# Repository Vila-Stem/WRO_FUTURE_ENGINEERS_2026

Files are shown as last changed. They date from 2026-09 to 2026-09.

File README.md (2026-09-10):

# VILA-STEM 8’s repository
**This is the Vila-stem 8 repository for the 2026 season WRO Future Engineers challenge**

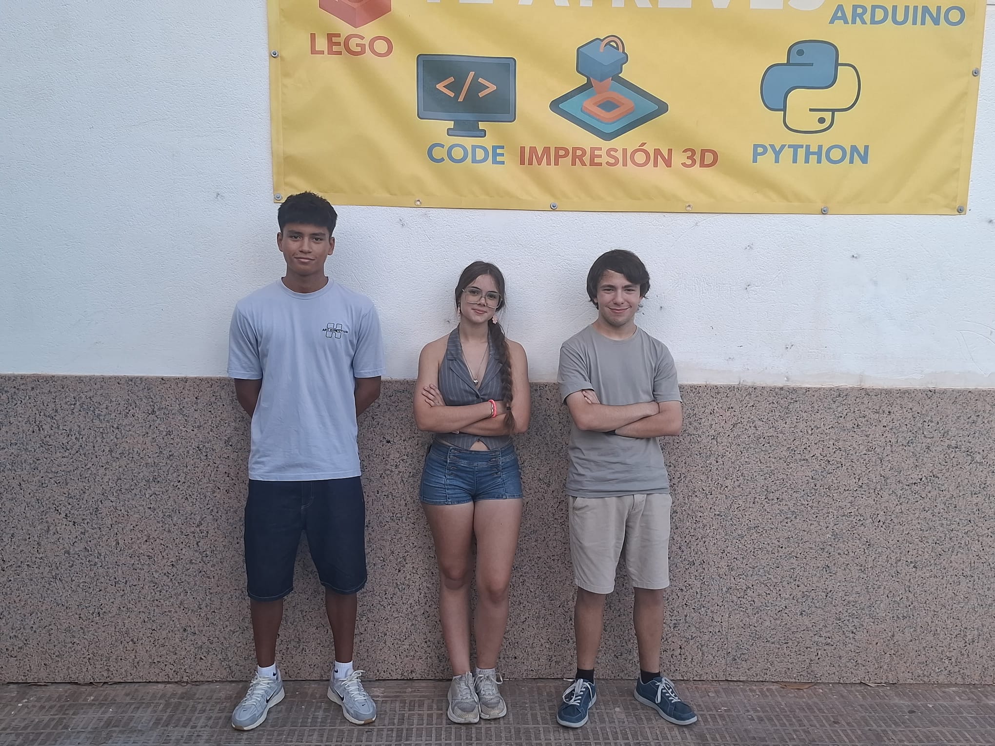
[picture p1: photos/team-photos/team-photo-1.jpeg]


## TABLE OF CONTENTS

* [1. INTRODUCTION](#1-introduction)

* [2. MOBILITY MANAGEMENT](#2-mobility-management)
    * [2.1. Chassis design](#21-chassis-design)
    * [2.2. How we arrived at this design](#22-how-we-arrived-at-this-design)
    * [2.3. Drive System](#23-drive-system)
    * [2.4. Steering System](#24-steering-system)

* [3. SENSORS AND ELECTRICITY](#3-sensors-and-electricity)
    * [3.1. List of sensors and electrical components](#31-list-of-sensors-and-electrical-components)
    * [3.2. Electrical diagram](#32-electrical-diagram)
    * [3.3. Connection type diagram](#33-connection-type-diagram)
    * [3.4. Power consumption](#34-power-consumption)

* [4. CODE](#4-code)

* [5. PHOTOS](#5-photos)
    * [5.1. Robot photos](#51-robot-photos)
    * [5.2. Team photos](#52-team-photos)

* [6. VIDEOS](#6-videos)

* [7. LIST OF COMPONENTS](#7-list-of-components)

* [8. LICENSE](#8-license)

* [9. ENGINEERING JOURNAL](#9-engineering-journal)

## 1. INTRODUCTION

Vila-stem 8 is the Future Engineers team of the Vila-Stem educational robotics cultural association, located in Vila-real, Spain. Some members of this team have already participated in the WRO in different categories in previous years, including this year, while for others it is their first time competing, but we are all equally excited to participate in the Future Engineers category of WRO 2026.

Our first competition this season was the regional WRO in Dénia, where we won first place and qualified for the national final.

Now we are heading to the national final of WRO Spain 2026 in Andorra, eager to present our project.

Throughout this document, you will find an explanation of our robot and links to other documents that explain the different sections in more detail.

To comply with the competition rules, we have also included a [**Engineering Journal**](/engineering-journal.pdf) in PDF format. This document is a compilation of the information explained throughout this repository.

## 2. MOBILITY MANAGEMENT

### 2.1. Chassis design

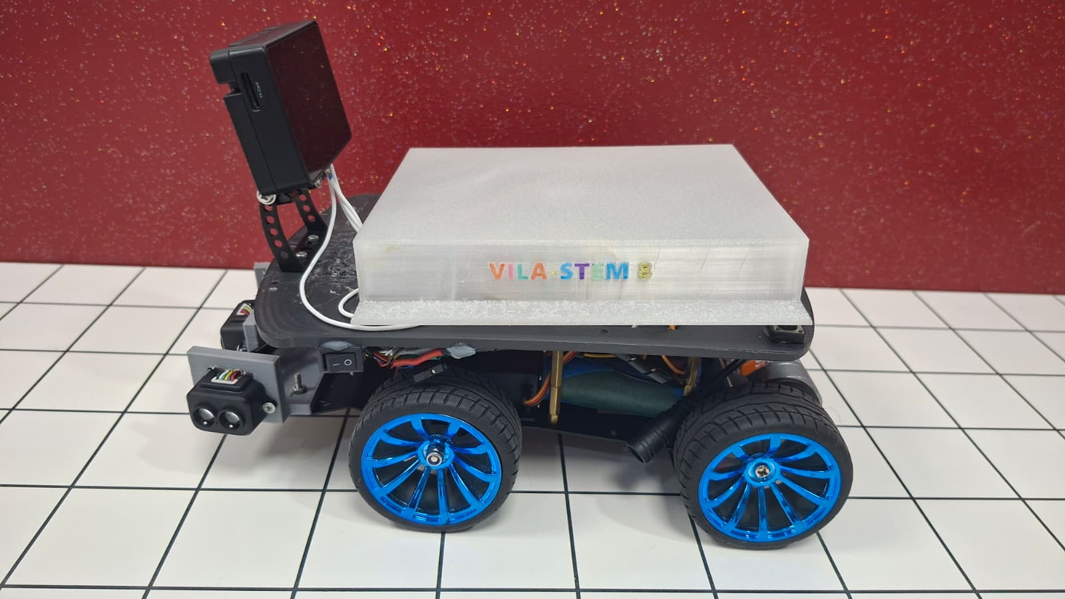
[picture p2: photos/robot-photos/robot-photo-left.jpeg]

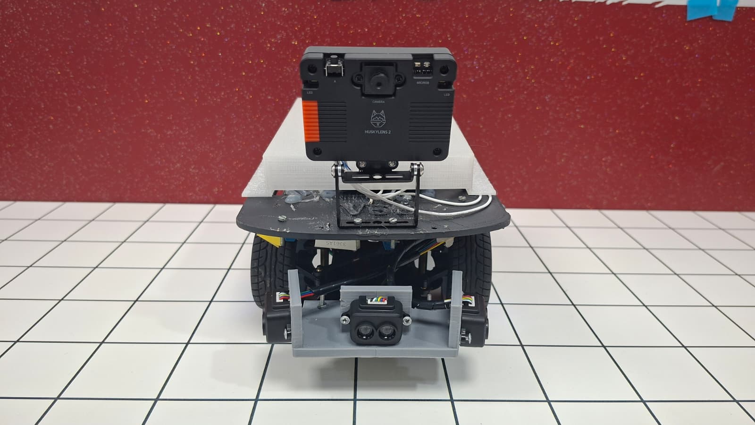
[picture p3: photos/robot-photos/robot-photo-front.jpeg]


The lower chassis base comes from a development kit we acquired, so we simply had to assemble it. This kit provided the wheels, motor, and steering system, which simplified assembly. We designed a top platform on top of this kit, where the components are installed, as well as another set of parts to mount the components.

Purchasing this kit allowed us to have a metal chassis that better withstands the robot's stresses. This freed us up to design, using plastic and 3D printing, those parts that wouldn't be subjected to heavy loads.

### 2.2. How we arrived at this design

Initially, the idea was to mount all the components on the lower chassis, but the lack of space and the desire for a more aesthetically pleasing design led us to install a top platform. This platform saves space and also provides easier access to the connections. We ruled out increasing the robot's height because this keeps the center of gravity low and maintains its compact size.

This year we also aimed for a more aesthetically pleasing robot, which is why the design includes, for example, a decorative top cover and insulated cable covers, among other improvements.

### 2.3. Drive System

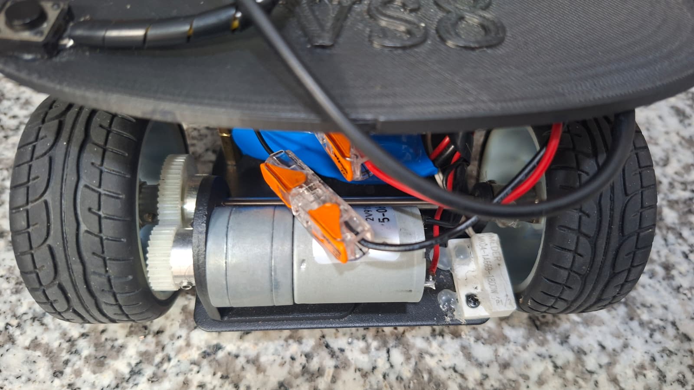
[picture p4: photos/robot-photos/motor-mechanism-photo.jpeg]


In our robot, the rear wheels are the drive wheels. There is a single axle connecting both wheels, and a gear connects them directly to the motor, without using any differential mechanism. This causes both wheels to always rotate at the same speed.

Although, theoretically, this mechanism could cause the wheels to slip on curves, since the path of travel is different for each wheel in this case, we chose this system because it seemed sufficient for our robot's needs and is easier to install and maintain. A more complex mechanism would have added an extra difficulty that, in the repeated tests we conducted, we didn't find necessary to implement. Any slippage does not affect the robot's proper functioning.

During assembly, we encountered some problems. Some gears and parts didn't fit together, and it took us a while to get them all aligned, but we eventually managed.

### 2.4. Steering System

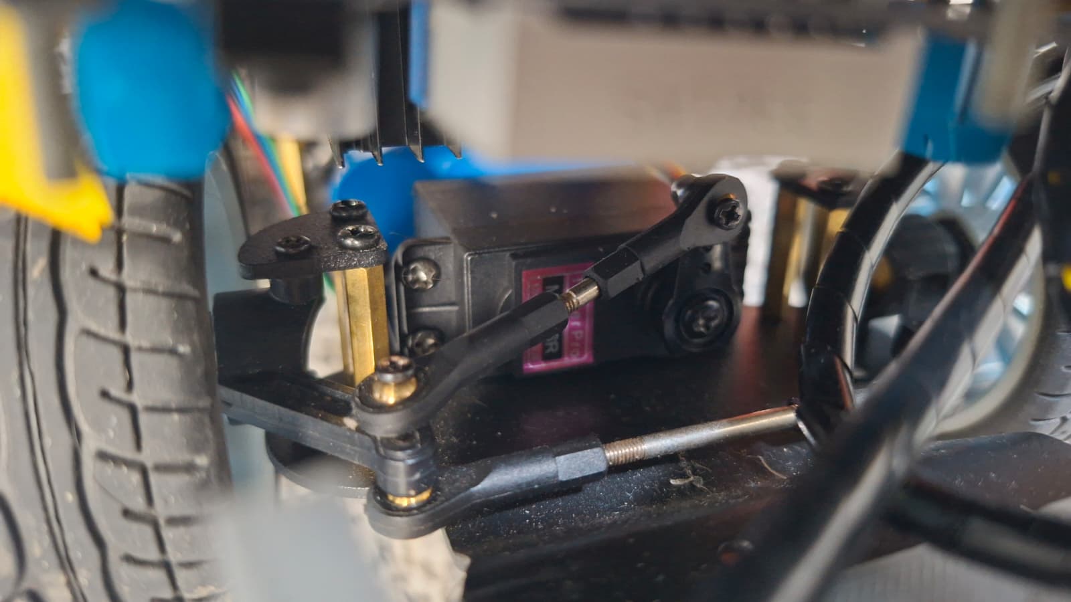
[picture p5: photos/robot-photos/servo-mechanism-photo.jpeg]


The steering system is the typical pivot axle (like a wagon): the entire front axle rotates on a central pin moved by the servo. It's the most common system, but it works just as well and is inexpensive, so it was the logical choice for us.

Here, too, we had problems, especially during assembly: some axle parts broke, and we had to replace them with identical ones. There were also parts that were difficult to fit, some because they weren't very well made and others because we got a little confused during assembly.

Physically, there isn't a stop that directly limits the servo's movement. However, the code itself includes limitations that would prevent the wheels from over-rotating and hitting the sides of the chassis.

## 3. SENSORS AND ELECTRICITY

The robot requires components for both control and power, as well as for obtaining the necessary information from the environment. This section will cover these components, why of their selection, and connection.

### 3.1. LIST OF SENSORS AND ELECTRICAL COMPONENTS

#### ESP32 S3



| | |
| --- | --- |
| **WHY:** | We chose an ESP32 over options like an Arduino because of the versatility of its GPIO pins, which allow us to freely configure almost all of them for functions such as I2C or UART communication, or for use as PWM. Furthermore, the ESP32 is already a fairly mainstream microcontroller, so there is ample information and libraries available online, simplifying our work. Of the different ESP32 variations for our main microcontroller, we chose the ESP32 S3 because it is newer, has extra pins, and more RAM, SRAM, and ROM capacity. However, a standard ESP32 could have also served our purpose with minor adjustments. |
| **LOCATION:** | The microcontroller is located on the top platform, under the upper trim cover. It is connected to an expansion board, which facilitates connecting and replacing components. |
| **VOLTAGE:** | 3.3V (can be powered via a 5V pin connected to a linear regulator) |

----

#### HUSKYLENS 2

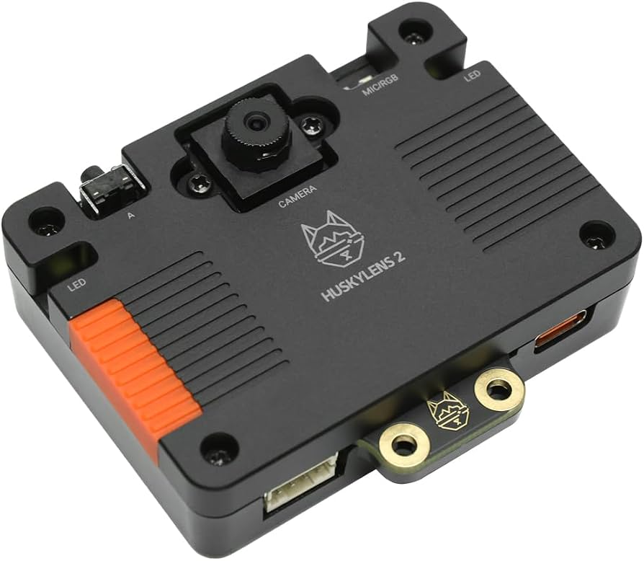
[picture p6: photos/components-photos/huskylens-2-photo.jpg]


| | |
| --- | --- |
| **WHY:** | For much of the robot's development, we tried using an ESP32 S3 CAM with a special lens. We originally chose this option because we thought it would be simpler than using a Huskylens 2, and because our experience with the Huskylens 1 had already been complicated. However, as development progressed, we realized it was actually much more complex. With the ESP32 S3 CAM, we had to manually calibrate several values per code for it to detect colors, and the detection algorithms weren't very effective. In contrast, after some tests with the Huskylens 2, we saw that its ability to be calibrated using the built-in screen and button, along with its improved color detection algorithms, led us to choose it. We had to adapt part of the obstacle code to this new sensor. |
| **LOCATION:** | It is located on the front of the robot, it has an special stand that keeps it above the robot and looking with a small angle down.|
| **VOLTAGE:** | 5V (can also be powered via 3.3V) |
| **CONNECTION TYPE:** | I2C |

----

#### L298N MOTOR DRIVER



| | |
| --- | --- |
| **WHY:** | We chose this motor driver because we already had it in the classroom, it generally delivers good results, and it's inexpensive and readily available should we need replacements. In the future, we would like to test the TB6612FNG, as we know it also offers good or even better results and takes up less space. In any case, the L298 motor has not presented any problems in all the tests performed and is easy to operate. |
| **LOCATION:** | It is located on the underside of the robot's upper platform. |
| **MOTOR VOLTAGE:** | 12V |
| **LOGIC VOLTAGE:** | 5V (In our case, it is obtained through a linear regulator from the 12V motor voltage) |
| **CONNECTION TYPE:** | PWM (speed control), 2 pins (to control the motor's direction or brake) |

---

#### MOTOR

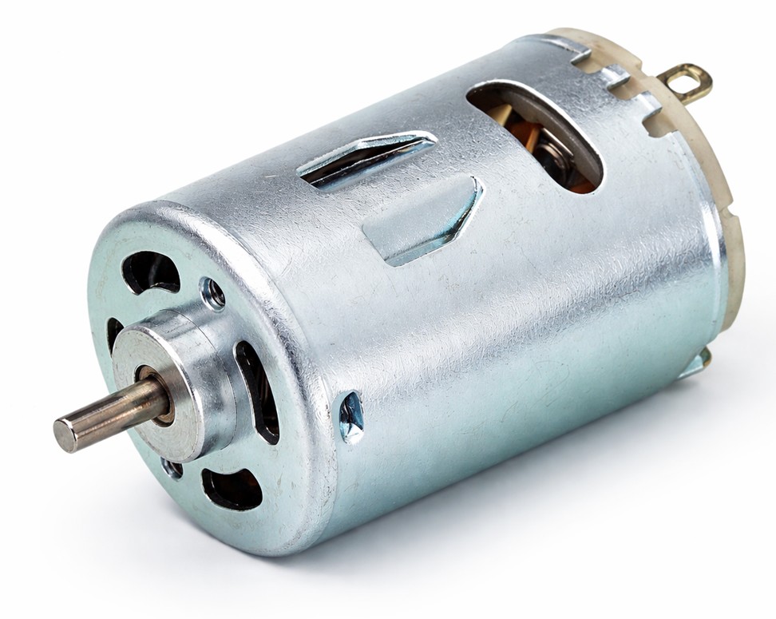
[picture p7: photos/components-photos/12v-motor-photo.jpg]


| | |
| --- | --- |
| **WHY:** | This motor is a 12V DC motor. Initially, we tested it because it was the one we already had in class, and we wanted to avoid buying new motors if the one we already had was working. It is true that this motor is somewhat bulky compared to other alternatives, but in previous, heavier projects, it never presented any torque or power problems, and the robot was already planned to be somewhat bulky, so we thought it would be a good option. The robot's speed isn't a major concern for us, as the time taken to complete the challenges is low on the tie-breaking priority list in the rules. |
| **LOCATION:** | On the back of the robot's lower platform. |
| **VOLTAGE:** | 12V |

---

#### TF-LUNA

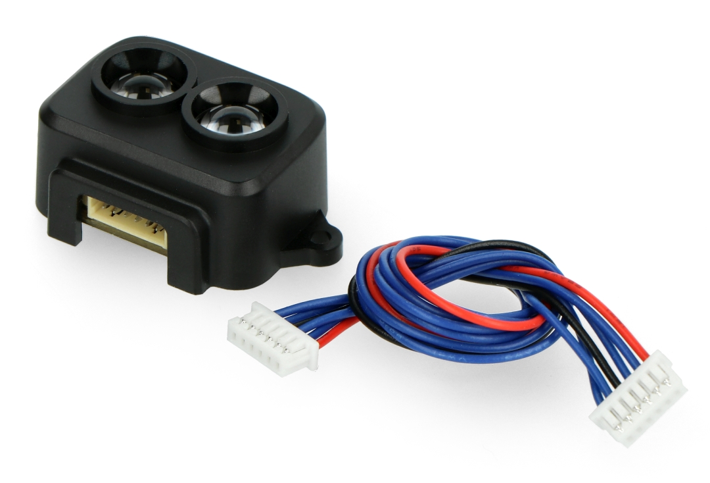
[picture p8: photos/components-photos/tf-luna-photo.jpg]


| | |
| --- | --- |
| **WHY:** | To complete the missions, it's essential to know the robot's position relative to the walls. This requires considering the robot's distance from the walls. There are several types of distance sensors: On the one hand, ultrasonic sensors are quite simple, inexpensive, and easy to find, but they offer low accuracy and vary significantly over long distances, which caused us considerable problems in this same challenge last year. Therefore, we quickly ruled them out. Another option is to use Time-of-Flight (ToF) sensors. These sensors emit a beam of light and calculate the time between its emission, reflection, and return, allowing for precise determination of the distance to the reflected object, since the speed of light is constant. We noticed that many WRO projects use a rotating ToF sensor called LiDAR. After conducting some tests with a LiDAR we had and reading reviews from others who had worked with this sensor, we found it difficult to use, so we ruled out LiDAR. Finally, we selected fixed ToF sensors, the TF-Luna. The TF-Luna is relatively inexpensive, and after our initial testing, we found it to be quite accurate. Specifically, we tested it by measuring multiple distances between 5 cm and 3 m (dimensions designed for the Future Engineers challenge), and in every case, the distance obtained with the TF-Luna perfectly matched the physical measurement taken with a meter stick. |
| **LOCATION:** | We have three sensors, one on each front side and one at the front. The side sensors are angled slightly forward. These sensors are mounted on a specially designed bracket and anchored to the lower platform. |
| **VOLTAGE:** | 5V |
| **CONNECTION TYPE:** | I2C |

---

#### ADAFRUIT TCS34725

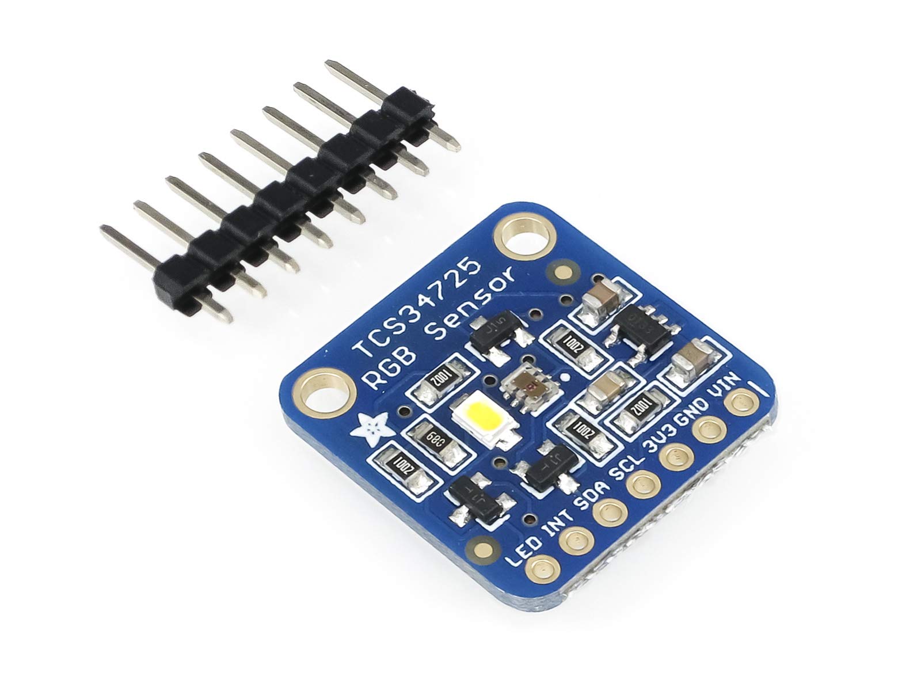
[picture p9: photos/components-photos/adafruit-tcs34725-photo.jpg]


| | |
| --- | --- |
| **WHY:** | To determine the robot's position on the board and the number of sections traversed, we use orange lines conveniently placed at the corners of the board. We measure the robot's movement over these lines using this color sensor. We chose this sensor after finding positive online reviews and because it offered an I2C connection. Before using it, we calibrated it, and after testing, we found it to be reliable and accurate, so we kept it. |
| **LOCATION:** | The lower platform has a hole facing the floor for the color sensor. |
| **VOLTAGE:** | 3.3V |
| **CONNECTION TYPE:** | I2C |

---

#### MG995 SERVOMOTOR

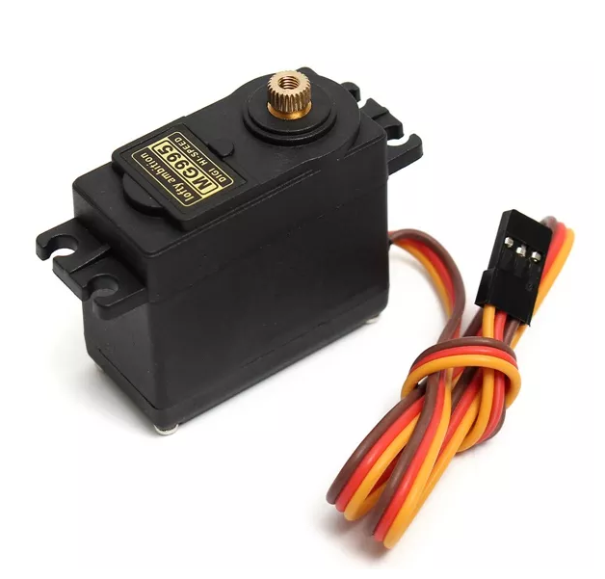
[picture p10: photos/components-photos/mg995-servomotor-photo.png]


| | |
| --- | --- |
| **WHY:** | A servomotor is necessary to control the steering of the front wheels. This servomotor was chosen because it offers higher torque (9.4 kg/cm) compared to other popular options like the SG90 (1.8 kg/cm), while maintaining a relatively low price and good availability. Price is a particularly important factor in this case, as our experience competing in this category shows that servomotors tend to wear out considerably during training and competition, requiring frequent replacement. Therefore, we prioritized a good price. |
| **LOCATION:** | On the lower platform. |
| **VOLTAGE:** | 5V |
| **CONNECTION TYPE:** | I2C |

---

#### LM2596 CONVERTERS

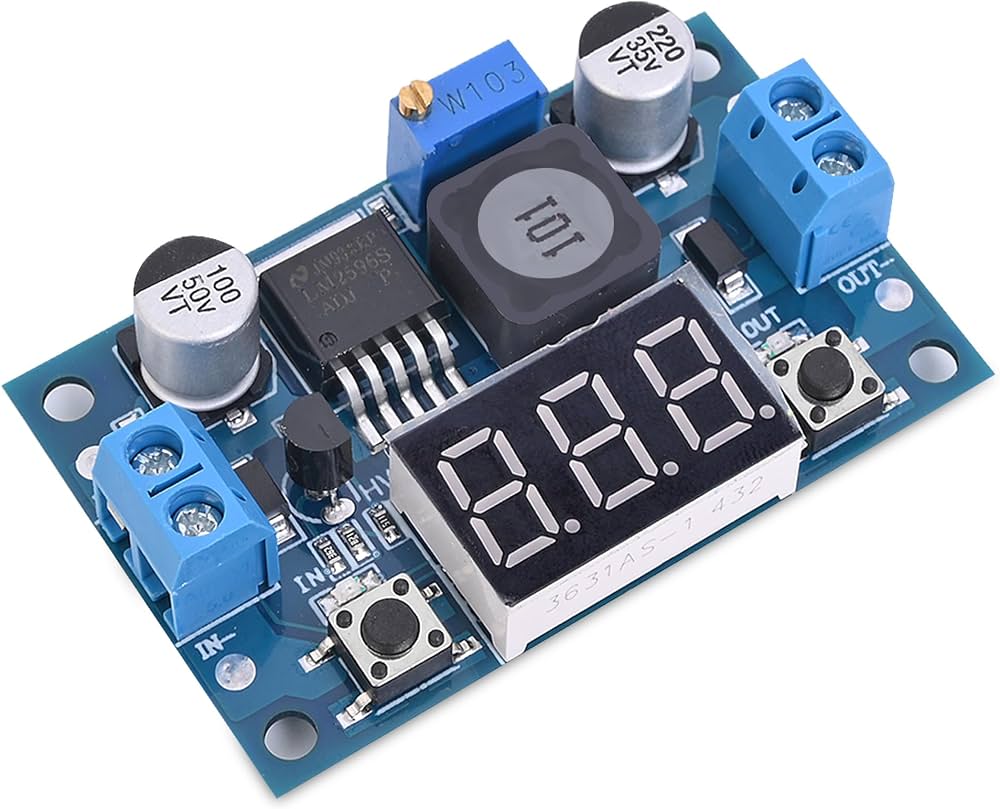
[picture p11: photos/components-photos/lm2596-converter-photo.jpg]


| | |
| --- | --- |
| **WHY:** | The 12V we get from the battery needs to be converted to 5V and 3.3V for the other components to function. This requires a converter. There are mainly two types: linear and switched-mode. Linear converters, like the LM7805, have the problem of being energy inefficient and generating a lot of heat when converting excess voltage. On the other hand, switched-mode converters offer higher efficiency and generate less heat. Therefore, we selected a switched-mode voltage converter. The advantage of choosing this particular version of the LM2596 is that it is adjustable, which allows us to have several identical converters in stock to meet the robot's needs. It also has a display that shows the output voltage in real time, useful for monitoring the power status without needing a multimeter. We have 2 12V to 5V converters because after installing the Huskylens 2 we saw that amount of current it used exceded the limits and made the voltage drop to the point that all the components connected to the only 5V converter stopped working, so we added one 12V to 5V only for the Huskylens 2 and another for all the rest of components.|
| **LOCATION:** | 2 are located on the underside of the robot's upper platform and the Huskylens 2 5V converter is located on top of the robot's upper platform. |

---

#### SWITCH

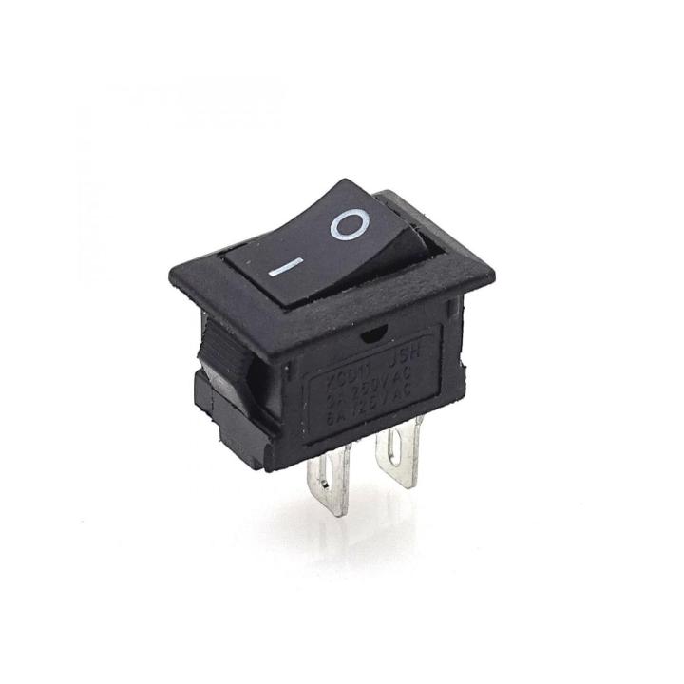
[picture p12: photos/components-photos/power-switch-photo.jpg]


| | |
| --- | --- |
| **WHY:** | According to regulations, a switch is required to cut off or activate the robot's power. |
| **LOCATION:** | On the side of the robot's upper platform. |

---

#### BUTTON



| | |
| --- | --- |
| **WHY:** | According to regulations, a separate button is required to activate the robot's execution of the challenge. |
| **LOCATION:** | On the robot's upper platform. |

### 3.2. ELECTRICAL DIAGRAM

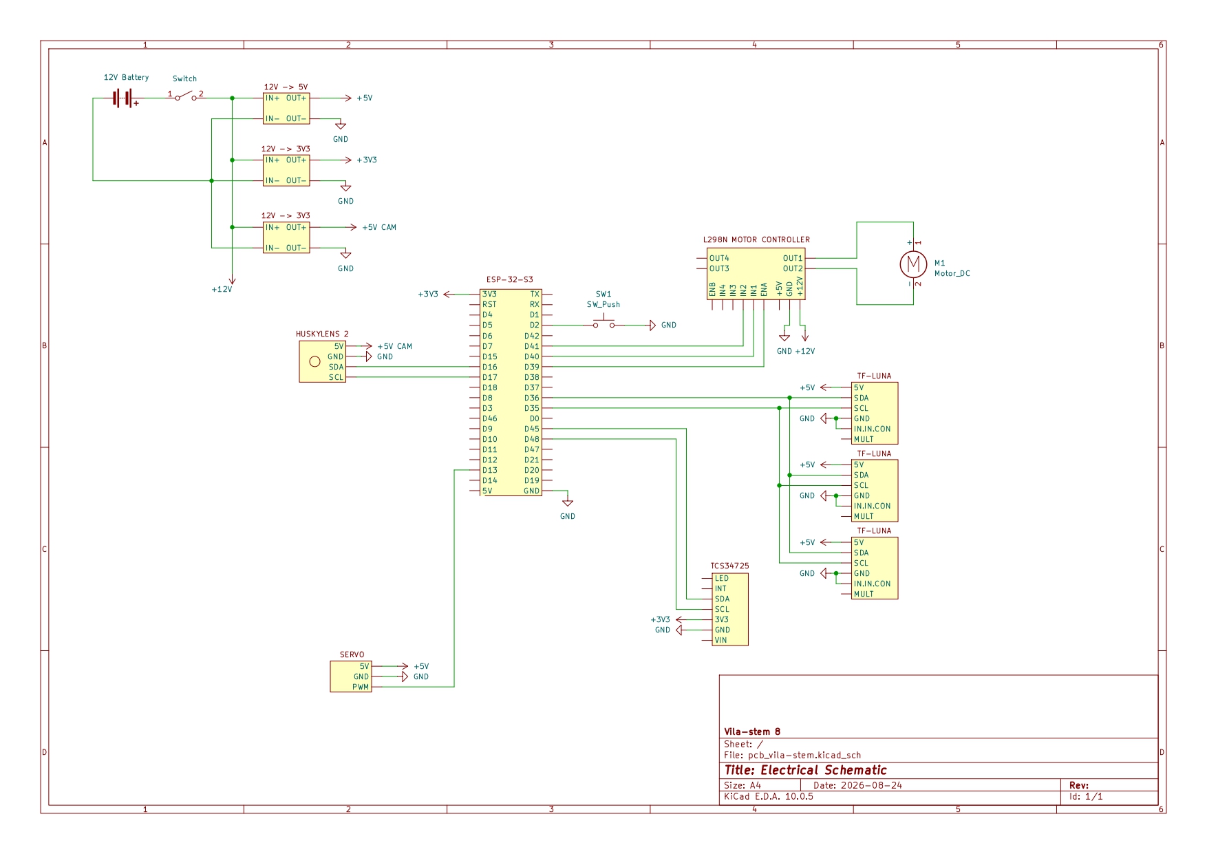
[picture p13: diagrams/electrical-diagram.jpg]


### 3.3. CONNECTION TYPE DIAGRAM

This diagram shows the connection type of each component to the main microcontroller. The pink squares represent the microcontroller. The blue octagons are the sensors that send information to the main microcontroller. The yellow circles are the actuators.

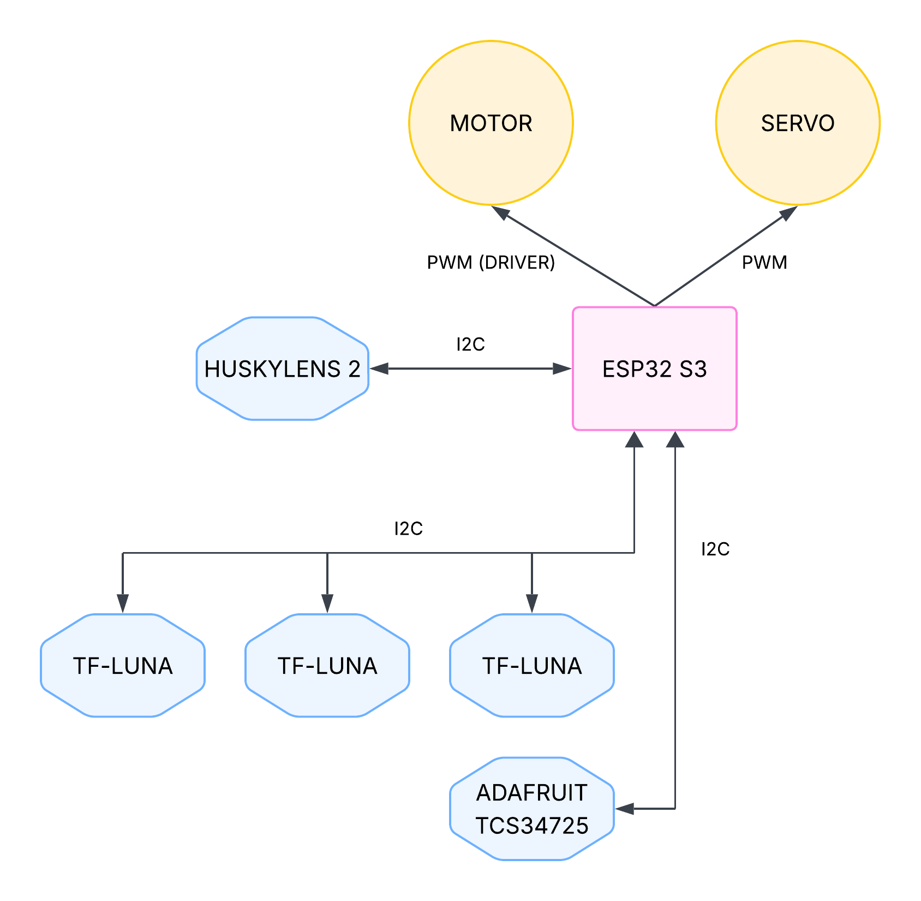
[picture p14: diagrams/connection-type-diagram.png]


### 3.4. POWER CONSUMPTION

| COMPONENT | VOLTAGE (V) | CURRENT (mA) |
| --- | ---: | ---: |
| 3 * LM2596 Converters | 12 | 50 |
| Servomotor MG995 | 5 | ≈ 200 - 1200 |
| Adafruit TCS34725 | 3.3 | 10 |
| Motor | 12 | ≈ 300 |
| 3 * TF-Luna | 5 | 70 |
| L298N Motor driver | Vm.: 12; Vlog.: 5 | 36 |
| Huskylens 2 | 5 | ≈ 300 - 600 |
| ESP32 S3 | 3.3 | ≈ 50 |

## 4. CODE

We can find a description of the operation and algorithms of the different codes by clicking on the following links.

- [**Open Challenge**](/code/open-challenge/): ESP32 main code for the Open Challenge
- [**Obstacle Challenge**](/code/obstacle-challenge/): ESP32 main code for the Obstacle Challenge

This diagram shows what code needs to be uploaded to the microcontroller.

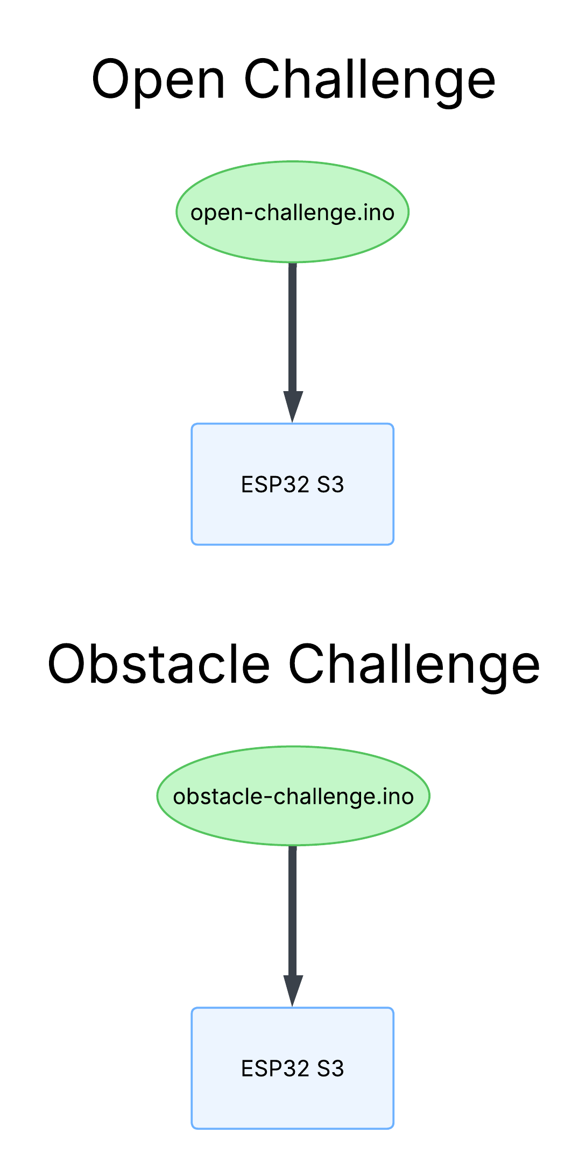
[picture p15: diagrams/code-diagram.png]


## 5. PHOTOS

### 5.1. ROBOT PHOTOS

| | |
| --- | --- |
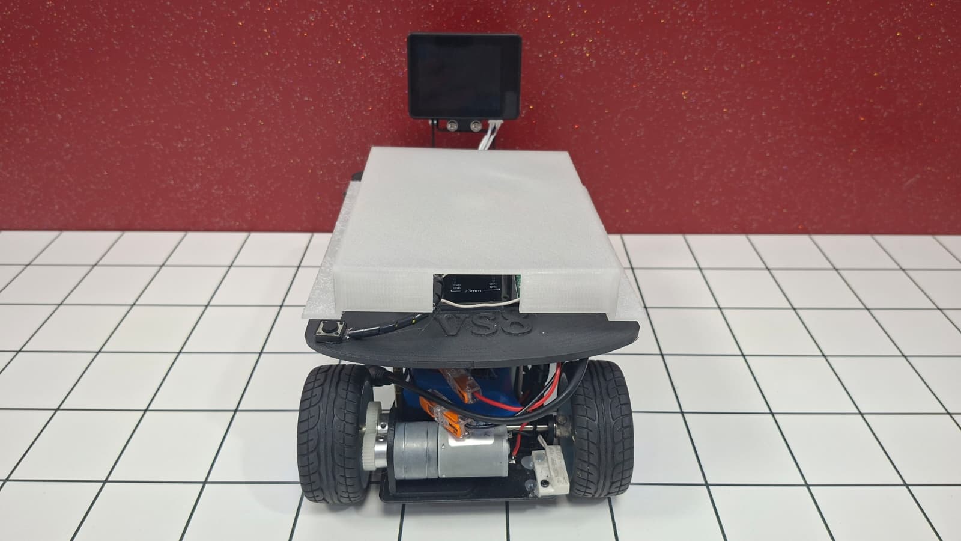
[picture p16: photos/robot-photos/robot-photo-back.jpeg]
|  |  |
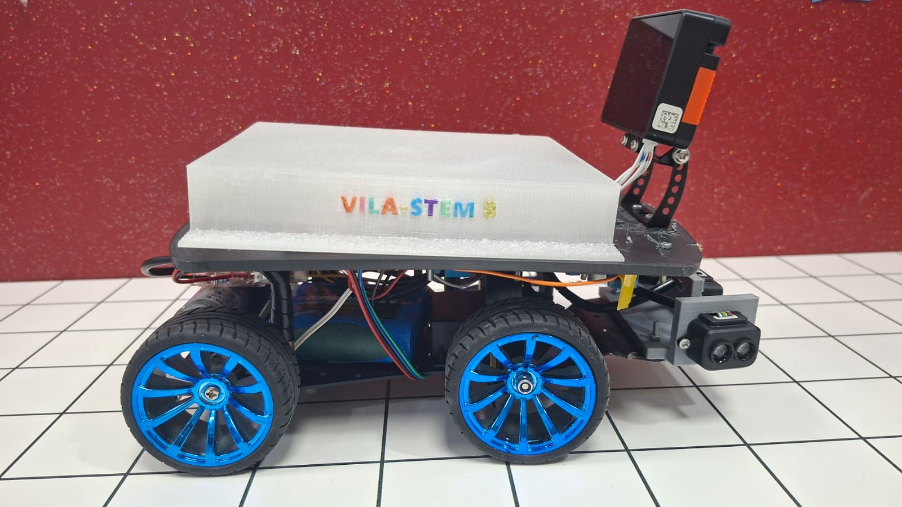
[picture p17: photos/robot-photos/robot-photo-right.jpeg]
|  |  |
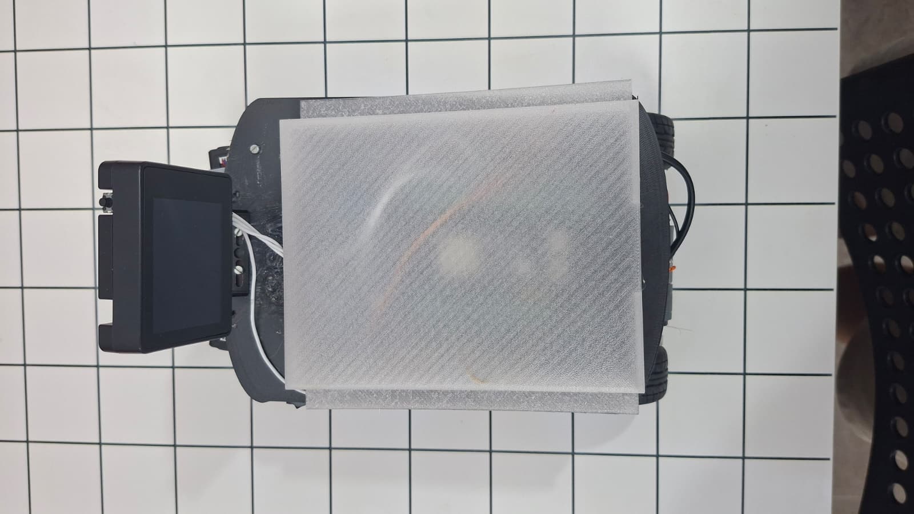
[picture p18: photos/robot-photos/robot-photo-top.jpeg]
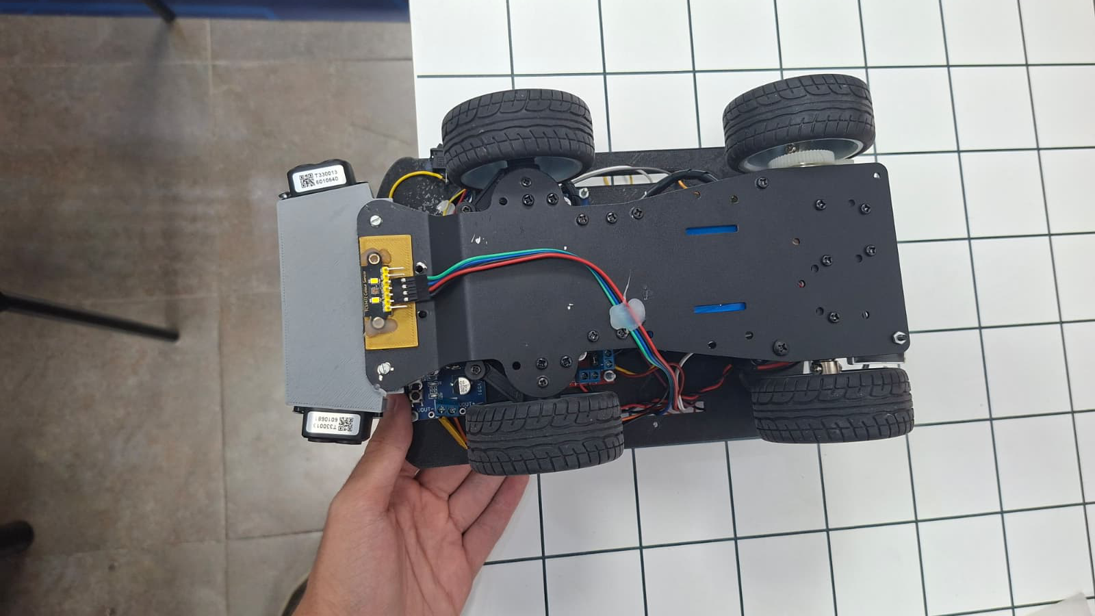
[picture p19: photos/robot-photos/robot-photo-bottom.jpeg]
|  |  |

### 5.2. TEAM PHOTOS



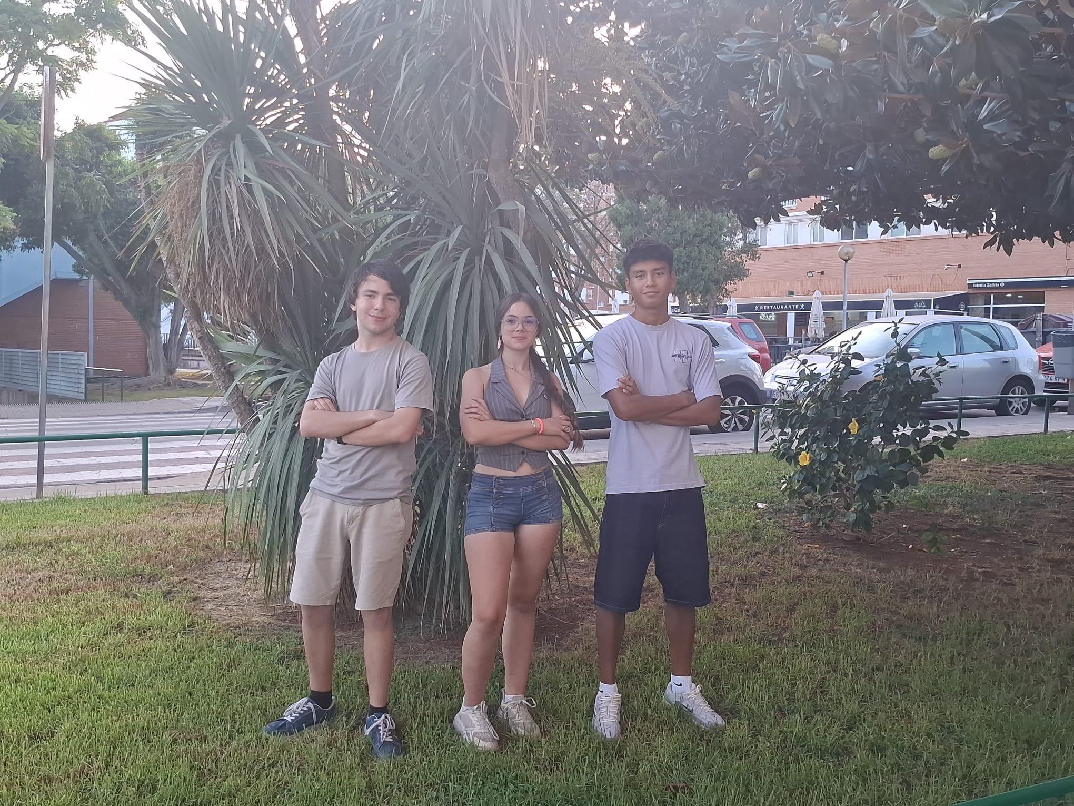
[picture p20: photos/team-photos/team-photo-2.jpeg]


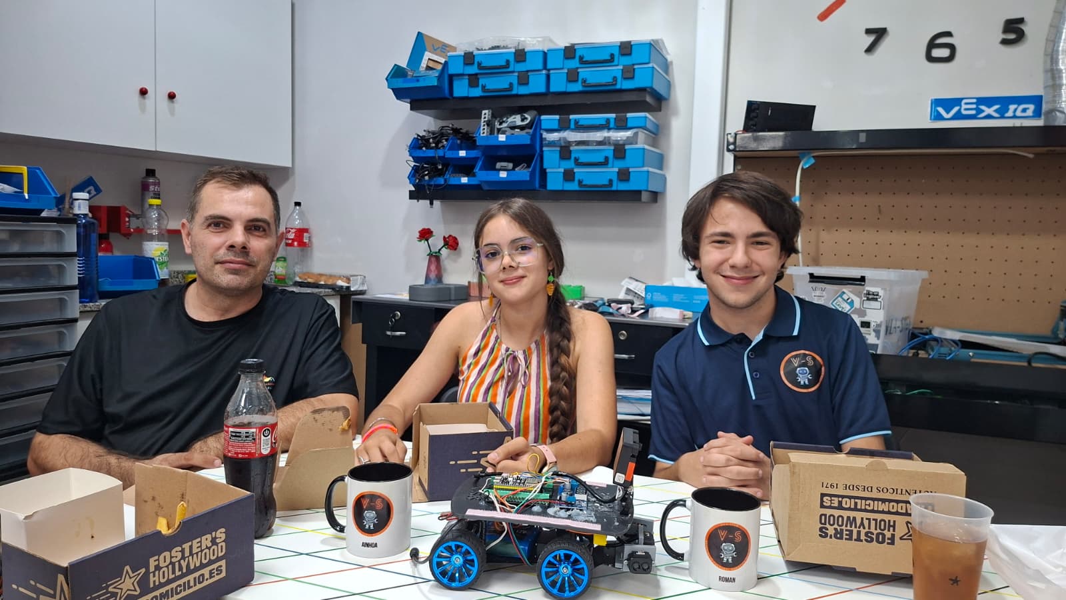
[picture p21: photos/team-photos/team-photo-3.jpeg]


## 6. VIDEOS

We have uploaded two videos showing our robot completing each challenge. You can access them via the following links:
* [Open Challenge](https://youtu.be/gIDQgGI8u58)
* [Obstacle Challenge](https://www.youtube.com/watch?v=H1E48MxDFis)

## 7. LIST OF COMPONENTS

* **3 * LM2596 Converters**
* **1 * Servomotor MG995** 
* **1 * Adafruit TCS34725** 
* **1 * 12V DC Motor** 
* **3 * TF-Luna** 
* **1 * LM2596 Converters**
* **1 * Huskylens 2**
* **1 * OV5640**
* **1 * ESP32 S3**

## 8. LICENSE

The code in this repository is licensed under the GNU General Public License v3.0.

Everything not under the GNU General Public License v3.0 in this repository (including photographs, diagrams, etc) is under the Creative Commons Attribution Share Alike 4.0 International license

A copy of each license can be found in the [LICENSE](LICENSE.txt) file.

## 9. ENGINEERING JOURNAL

As we mentionad on the introduction, to comply with the competition rules, we have also included a [**Engineering Journal**](/engineering-journal.pdf) in PDF format. This document is a compilation of the information explained throughout this repository.

We highly recommend to check out this document, as it is a better looking version of what can be found here at the repository and easier to use.

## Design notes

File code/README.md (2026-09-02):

# CODE

In this folder you can find the various codes for the robot's operation.

- [**Open Challenge**](/code/open-challenge/): ESP32 main code for the Open Challenge
- [**Obstacle Challenge**](/code/obstacle-challenge/): ESP32 main code for the Obstacle Challenge



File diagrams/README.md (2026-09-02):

# Diagrams

This folder contains the multiple diagrams used to documentate the project.

### Code diagram

Shows what code has to be uploaded to the ESP32 S3 on each challenge.



### Connection type diagram

This diagram shows the connection type of each component to the main microcontroller. The pink squares represent the microcontroller. The blue octagons are the sensors that send information to the main microcontroller. The yellow circles are the actuators.



### Electrical diagram

Component connections.



### Open challenge flowchart

Shows the algorithm used in the open challenge main code.

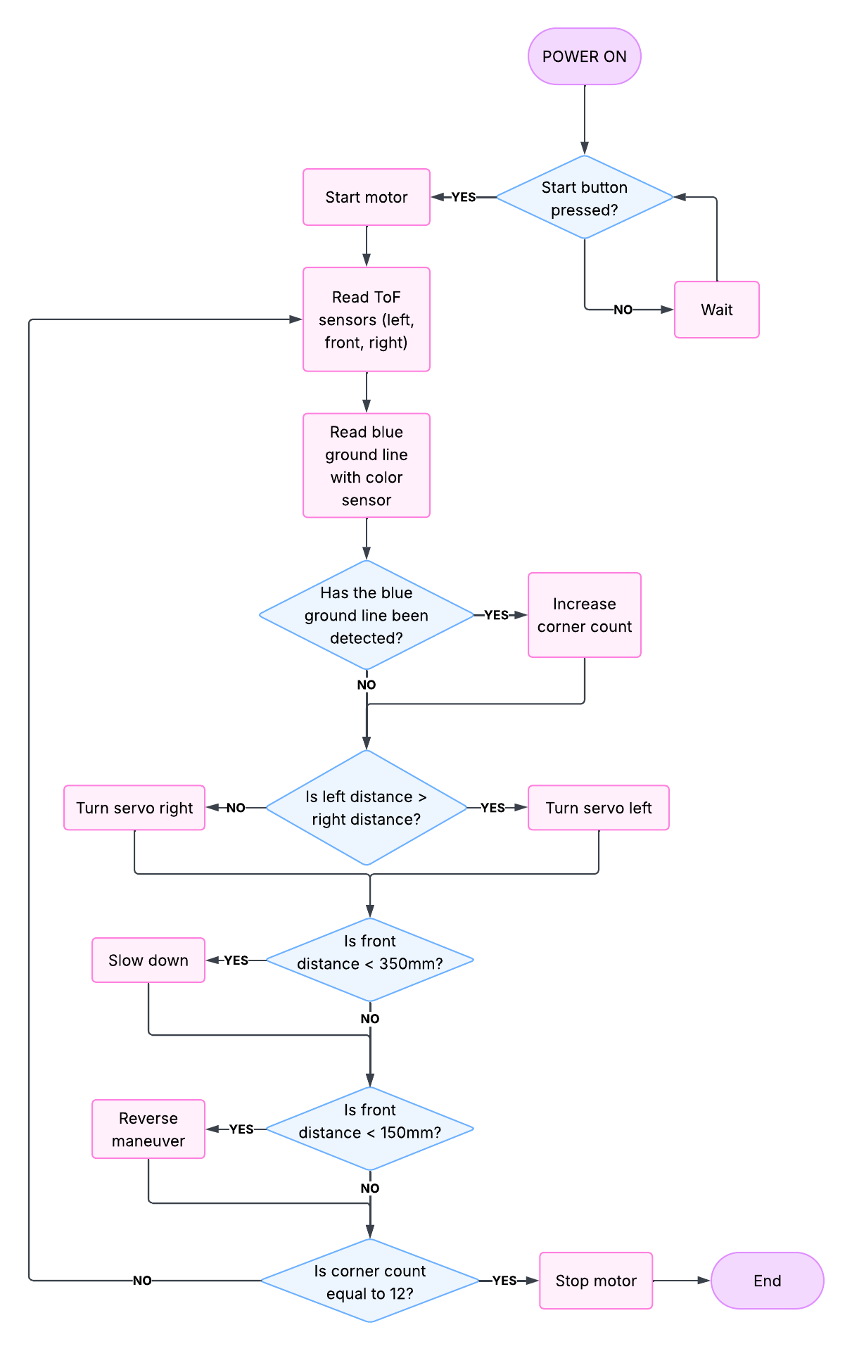
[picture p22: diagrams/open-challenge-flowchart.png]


### Obstacle challenge flowchart

Shows the algorithm used in the obstacle challenge main code.

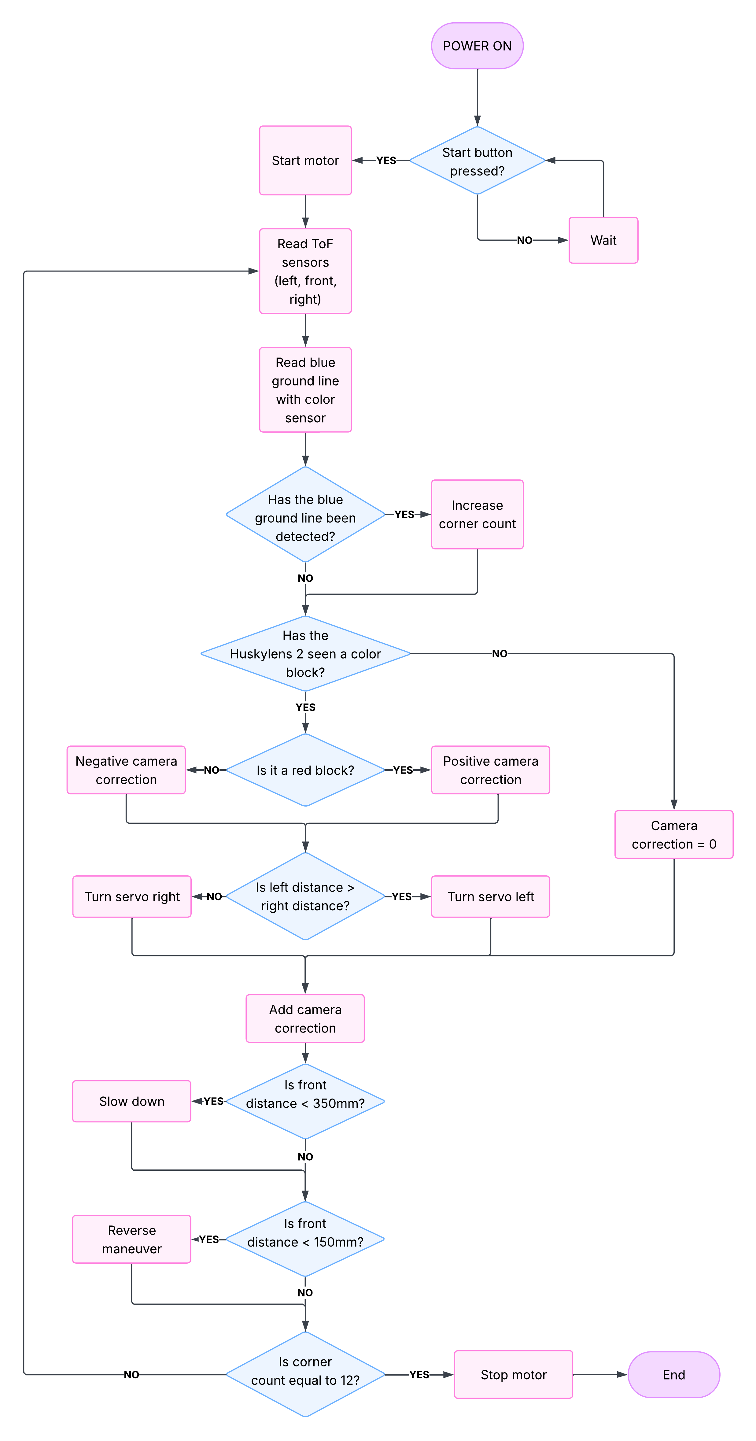
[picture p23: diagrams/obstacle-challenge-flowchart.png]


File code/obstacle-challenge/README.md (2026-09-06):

# obstacle-challenge.ino

# Introduction to the code

We strongly recommend that you first study the code of the [**Open Challenge**](/code/open-challenge/) to understand how the different functions work and then come to this chapter, because in order not to unnecessarily repeat the explanations we will simplify those already explained.

# Code structure

All the code for this challenge is contained in a single .ino file, named obstacle-challenge.ino. This code is executed in the robot's ESP32 main.

There are no other programs for this challenge.

We have not created any additional libraries or files as required.

# Algorithm design

A flowchart of the code's operation can be seen below.



As can be seen, as soon as the robot is powered on, it enters standby mode until the Start button is pressed. Meanwhile, as observed in the source code, the robot's various systems and peripherals are initialized (Huskylens 2, I2C communication, color sensor, servomotor, etc.).

Once the Start button is pressed, the robot enters the loop. We can divide the loop's operation into three parts:
1. Robot Movement
2. Limit Case Checking
3. Camera analysis

## Robot movement

The basic movement strategy is the same as in the Open Challenge: use the side TF-Luna sensors to keep the robot as centered as possible between the side walls of the track. In fact, if the Obstacle Challenge were to occur without any traffic signs, the robot would complete the challenge in the same way as in the Open Challenge.

Building on the foundation already explained, the sign avoidance mechanism is added. This involves using information received from the camera (block type, position, etc.) and the block's X-axis position to add a correction to the servo's rotation angle, depending on the block's color. For example, if a green block is encountered slightly to the right of the robot, a slight servo offset will be added so that the wheels turn a little more to the left than they would if there were no block. Conversely, if a red block is encountered far to the right of the robot, a large offset will be added so that the robot can avoid the blocks.

The basic strategy was already tested during the Open Challenge trials. The obstacle section involved trial and error until it worked. The biggest problems we encountered were related to the block detection mechanism, which we explain below, rather than the dodge mechanism.

## Check of limit cases

The loop also performs certain checks at all times on the following things, as shown in the flowchart:
- If the color sensor facing the ground detects the blue line, then the internal counter corner_count, which measures how many corners the robot has passed through, is incremented by one. This tells us how many sections the robot has traversed.
- If the front Luna ToF sensor measures a distance less than 350mm, the motor speed is reduced to avoid a collision. This can sometimes happen when getting too close to walls.
- If the front Luna ToF sensor measures a distance less than 150mm, a collision is practically imminent, and the reversing process is activated. This temporarily disables the robot's movement and makes it reverse to avoid getting stuck.
- If the corner_counter is equal to 12, the robot has already completed three laps and must stop in the final section.

## Camera analysis

First, regarding the camera analysis, it's worth noting that the Huskylens 2 wasn't our first choice, as explained in the electronics and sensors section. However, introducing the Huskylens 2 allowed us to delegate some of the detection and calibration algorithms to those already integrated into the camera, thus improving the code's reliability and ease of use.

We utilize the Huskylens 2's color detection algorithm, as it detects blocks of color, which is precisely what we needed. The ESP32S3 constantly queries what the Huskylens 2 is seeing, obtaining certain data from each block it detects. Internally, we then select the largest block, which will be the closest to the camera. This way, if it detects two signals, one near and one far, it first acts on the nearer one.

Once the block is selected, we send its color and X position relative to the robot to the main code, so the movement algorithm can handle the rest.

To calibrate the camera to the colors, we used the color training functionality already available on the Huskylens 2, accessible via the screen and a button. In the various tests we conducted, we found that compared to the Huskylens 1 (which we also had at the academy), the Huskylens 2 is much better at distinguishing colors and seeing the same color in different lighting environments. This is ideal because we cannot guarantee that the lighting will be constant across the entire board on competition day, and this way, even if one part is brighter than another, it will see the correct color in all cases.

# Bugs and errors found in the code

In terms of movement, since we based our work on the already functional Open Challenge code, we haven't encountered any particular bugs. We recommend reviewing that section to see what might be causing problems.

Some errors already related to this challenge include typical wiring mistakes, such as incorrectly connecting the TX and RX pins. We'd like to highlight these main issues that bothered us the most:
- One problem we observed after extensive testing is that the wheel servos wear out quite quickly, requiring frequent replacement. There's no single solution, as wear is common with any machine; however, adapting to this wear is key. We've decided to purchase several spare servos to take with us to competitions. Furthermore, we've learned that if we redesign the robot in the future, we should make servo replacement easier. Currently, it's a bit difficult, but we don't have the time to redesign the entire mechanism.
- Another issue is that we originally used an ESP32 S3 CAM. This option is incredibly cheaper than using the Huskylens 2; however, after using it for a while, we found that calibrating it for our challenge was really difficult, since we had to manually manage nearly 10 values for each color and then manually change them via code, which was very time-consuming. This, combined with the fact that the detection algorithm we set up wasn't very good, led us to opt for the Huskylens 2.

# Source code description

## Functions

| | Name |
| --- | --- |
| uint16_t | **[LunaRead16](#function-lunaread16)**(uint8_t addr, uint8_t reg) |
| uint16_t | **[LunaDistance](#function-lunadistance)**(uint8_t addr) |
| void | **[Drive](#function-drive)**() |
| bool | **[InitHuskyLens](#function-inithuskylens)**() |
| bool | **[RequestHuskyLens](#function-requesthuskylens)**() |
| void | **[setup](#function-setup)**() |
| void | **[loop](#function-loop)**() |

## Constants

| | Name | Value |
| --- | --- | --- |
| const uint8_t | **LUNA_COUNT** <br>Number of Luna time of flight sensors| 3
| const uint8_t[LUNA_COUNT] | **LUNA_ADDR** <br>I2C address of each ToF sensor. Right, Left, Front | {0x11, 0x12, 0x13} |
| const uint16_t | **LUNA_STRENGHT_MIN** <br>Minimum strenght needed from the ToF sensor to accept a measurement | 20 |
| const uint16_t | **LUNA_CLOSE_STRENGTH** <br>Minumum strength needed to consider a 0 distance measurement too close | 150 |
| const uint16_t | **LUNA_CLOSE_MM** <br>Value (mm) used in case of a too close measurement | 150 |
| const uint16_t | **FRONT_BRAKE_MM** <br>Progressive braking start distance (mm) threshold | 350 |
| const uint16_t | **FRONT_REAR_MM** <br>Reverse gear start distance (mm) threshold | 150 |
| const int | **MOTOR_B_PIN**  | 20 |
| const int | **MOTOR_A_PIN**  | 10 |
| const int | **ENA_PIN**  | 15 |
| const int | **BUTTON_PIN**  | 13 | 
| const int | **ODOMETER_PIN**  | 15 |
| const int | **SDA_PIN**  | 11 |
| const int | **SCL_PIN**  | 12 |
| const int | **SDA_PIN_COLOR** <br>SDA for TCS34725 and HuskyLens 2 | 40 |
| const int | **SCL_PIN_COLOR** <br>SCL for TCS34725 and HuskyLens 2 | 41 |
| const int | **SERVO_PIN**  | 9 |
| const int | **BASE_SPEED**  | 120 |
| const int | **HUSKYLENS_ADDR** <br>HuskyLens 2 I2C address | 0x50 |
| const int | **HUSKYLENS_TIMEOUT_MS** <br>Time it waits for HuskyLens response | 1000 |
| const int | **HUSKYLENS_ID_GREEN_1** <br>ID assigned to green in HuskyLens | 1 |
| const int | **HUSKYLENS_ID_GREEN_2** <br>ID assigned to green in HuskyLens | 3 |
| const int | **HUSKYLENS_ID_RED_1** <br>ID assigned to red in HuskyLens | 2 |
| const int | **HUSKYLENS_ID_RED_2** <br>ID assigned to red in HuskyLens | 4 |
| const int | **CAM_CLOSE_AREA** <br>Block area (width*height px) that means the object is too close and triggers reverse | 90000 |
| const int | **CAM_COUNT_NUMBER** <br>How many drive loops the camera correction has to be applied | 15 |
| const int | **CAM_CLOSE_NUMBER** <br>How many drive loops the block reverse flag has to be up | 8 |

## Variables

| | Name |
| --- | --- |
| Adafruit_TCS34725 | **tcs** <br>Color sensor TCS34725 object.  |
| Servo | **servo** <br>Servo object.  |
| int | **button_state** <br>START button state.  |
| int | **corner_count** <br>Counts the number of corners the robot has passed. It should go from 0 to 12.  |
| long | **delay_line** <br>NOT IN USE.  |
| int | **travel_sense** <br>Controls travel sense. 0 = BRAKE, 1 = FORWARD, 2 = BACKWARD.  |
| byte | **rear_phase** <br>Controls the rear phases. 0 = NORMAL, 1 = STOP, 2 = REVERSE, 3 = RESUME.  |
| long | **end_motor_millis** <br>Variable to control the additional time added from entering the last section until the motor stops.  |
| long | **prev_millis_line_detection** <br>Variable to control time and avoid multiple detections of the same line.  |
| long | **prev_millis_front** <br>Variable to control time and avoid multiple detections of the wall from the front sensor.  |
| unsigned long | **rear_phase_until** <br>Variable to control time for the reverse system.  |
| long | **odo_filter** <br>Variable to control time and avoid multiple detections of the same step of the odometer.  |
| int | **odo_integral** <br>Odometer step count.  |
| int | **d_servo** <br>How much the servo needs to move.  |

## Functions Documentation

### function LunaRead16

```cpp
uint16_t LunaRead16(uint8_t addr,uint8_t reg)
```

**Parameters**: 

  * **addr** I2C address of the ToF Luna that you wish to request 
  * **reg** Value to be requested. 0x00 for distance. 0x02 for strength 

**See**: [LunaDistance()](#function-lunadistance)

**Return**: Desired value of the ToF Luna in question 

Request the demanded value of the indicated ToF Luna via I2C connectivity. 

--------------

### function LunaDistance

```cpp
uint16_t LunaDistance(uint8_t addr)
```

**Parameters**: 

  * **addr** I2C address of the ToF Luna that you wish to request 

**See**: [LunaRead16()](#function-lunaread16)

**Return**: 

  * Distance in mm measured 
  * 0xFFFF if failed to measure 

This function returns the distance in mm measured by the requested Luna ToF and also ensures that this measurement makes sense using the strength of the Luna ToF, thus giving consistent results in borderline cases.

--------------

### function InitHuskyLens

```cpp
bool InitHuskyLens()
```

**Parameters**: 

  * **none** 

**See**: [RequestHuskyLens()](#function-requesthuskylens)

**Return**: 
  * true if initialization successful
  * false if initialization was unsuccessful

Initialize HuskyLens communication (shares Wire1 with the TCS34725). 

--------------

### function RequestHuskyLens()

```cpp
bool RequestHuskyLens()
```

**Parameters**: 

  * **none** 

**See**: [InitHuskyLens()](#function-inithuskylens)

**Return**: 
  * true if a valid green/red block was detected
  * false if otherwise

Request color and position data from HuskyLens and picks the largest detected color block and computes a servo correction.

--------------

### function Drive

```cpp
void Drive()
```

**Parameters**: 

  * **none** 

**See**: 

  * [LunaDistance()](#function-lunadistance)
  * [ServoTurning()](#function-servoturning)

**Return**: void 

The driving and collision avoidance algorith. 

--------------

### function setup

```cpp
void setup()
```

**Parameters**: 

  * **none** 

**Return**: void 

This code only runs once when the ESP32 starts up. Initialize all systems and peripherals and wait for the start button to be pressed to start the program. 

--------------

### function loop

```cpp
void loop()
```

**Parameters**: 

  * **none** 

**Return**: void 

This code only runs all the time. 

## Source code

```cpp
/***********************************************************************
 *  FILE NAME:  obstacle-challenge
 *
 *
 *  PURPOSE:    This program is the version of the main 
 *              robot code for the Obstacle Challenge of the 
 *              Future Engineers category of the World
 *              Robot Olympiad.
 *  
 *
 *  HOW IT WORKS: The program uses side time-of-flight 
 *                distance sensors to keep the robot 
 *                constantly aligned with the center line 
 *                between the two side walls. Additionally, 
 *                in the event of a frontal collision or 
 *                when approaching a collision, the front 
 *                sensor is used to move backward or reduce 
 *                speed, respectively. It is connected to a
 *                HuskyLens 2 that tells if there is an object,
 *                its position and color, so this code makes the 
 *                servo turn enough to pass the obstacle through
 *                the right side.
 *
 *
 *  LIBRARIES USED:
 *  Name                        Description
 *  ----                        -----------
 *  ESP32Servo                  Functions required to control a 
 *                               servomotor with the ESP32
 *  Wire                        Allows I2C communication
 *  Adafruit_TCS34725           Functions required to use the 
 *                               Adafruit TCS34725 RGB Color Sensor
 *  DFRobot_HuskylensV2         Functions for HuskyLens AI vision sensor
 *
 *
 *  OTHER PROGRAMS NEEDED TO WORK
 *  Name                        Description
 *  ----                        -----------
 *  none
 *
 *
 *  CREATED BY: Vila-Stem 8
 *                                                
 *  LAST MODIFIED: September 6th 2026                                     
 *                                                                      
 *                                                                      
 *  REPOSITORY: https://github.com/Vila-Stem/WRO_FUTURE_ENGINEERS_2026  
 *
 ***********************************************************************
*/

/* INCLUDE LIBRARIES */
#include <ESP32Servo.h>
#include <Wire.h>
#include <Adafruit_TCS34725.h>
#include "DFRobot_HuskylensV2.h"

/* CONSTANT VALUES */
/* Related to the Luna time of flight (ToF) sensor */
const uint8_t LUNA_COUNT = 3;                               ///< Number of Luna time of flight sensors
const uint8_t LUNA_ADDR[LUNA_COUNT] = {0x11, 0x12, 0x13};   ///< I2C address of each ToF sensor. Right, Left, Front
const uint16_t LUNA_STRENGHT_MIN = 20;                      ///< Minimum strenght needed from the ToF sensor to accept a measurement
const uint16_t LUNA_CLOSE_STRENGTH = 150;                   ///< Minumum strength needed to consider a 0 distance measurement too close
const uint16_t LUNA_CLOSE_MM = 150;                         ///< Value (mm) used in case of a too close measurement

/* Collision avoidance threshold distances */
const uint16_t FRONT_BRAKE_MM = 350;                        ///< Progressive braking start distance (mm) threshold
const uint16_t FRONT_REAR_MM = 150;                         ///< Reverse gear start distance (mm) threshold

/* Pins */
const int MOTOR_B_PIN = 20;
const int MOTOR_A_PIN = 10;
const int ENA_PIN = 15;                                     ///< Enabled motor pin. Used with PWM for speed control
const int BUTTON_PIN = 13;                                  ///< START button pin
const int SDA_PIN = 11;
const int SCL_PIN = 12;
const int SDA_PIN_COLOR = 40;                               ///< SDA for TCS34725 and HuskyLens 2
const int SCL_PIN_COLOR = 41;                               ///< SCL for TCS34725 and HuskyLens 2
const int SERVO_PIN = 9;

const int BASE_SPEED = 120;

/* Huskylens */
const int HUSKYLENS_ADDR = 0x50;                            ///< HuskyLens 2 I2C address
const int HUSKYLENS_TIMEOUT_MS = 1000;                      ///< Time it waits for HuskyLens response
const uint8_t HUSKYLENS_ID_GREEN_1 = 1;                     ///< ID assigned to green in HuskyLens
const uint8_t HUSKYLENS_ID_GREEN_2 = 3;                     ///< ID assigned to green in HuskyLens
const uint8_t HUSKYLENS_ID_RED_1 = 2;                       ///< ID assigned to red in HuskyLens
const uint8_t HUSKYLENS_ID_RED_2 = 4;                       ///< ID assigned to red in HuskyLens
const int CAM_CLOSE_AREA = 90000;                           ///< Block area (width*height px) that means the object is too close and triggers reverse
const int CAM_COUNT_NUMBER = 5;                             ///< How many drive loops the camera correction has to be applied (antes 7)
const int CAM_CLOSE_NUMBER = 8;                             ///< How many drive loops the block reverse flag has to be up
const int CAM_GREEN_GAIN = 4;
const int CAM_RED_GAIN = 8;
const uint8_t HUSKY_STABLE_COUNT = 2;                       ///< Consecutive detections required
const unsigned long HUSKY_MEMORY_MS = 250;                  ///< Keep last valid detection
// ALGORITHM_COLOR_RECOGNITION is defined by the HuskyLens library
// (value 4). This guard is only a safety net for library versions
// that do not expose it.
#ifndef ALGORITHM_COLOR_RECOGNITION
#define ALGORITHM_COLOR_RECOGNITION 4
#endif

/* CREATE OBJECTS */
Adafruit_TCS34725 tcs = Adafruit_TCS34725(TCS34725_INTEGRATIONTIME_50MS, TCS34725_GAIN_60X);
Servo servo;
HuskylensV2 huskylens;

/* VARIABLES */
int button_state = HIGH;              ///< START button state
int corner_count = 0;                 ///< Counts the number of corners the robot has passed. It should go from 0 to 12.
long delay_line = 0;                  ///< NOT IN USE
int travel_sense = 1;                 ///< Controls travel sense. 0 = BRAKE, 1 = FORWARD, 2 = BACKWARD
byte rear_phase = 0;                  ///< Controls the rear phases. 0 = NORMAL, 1 = STOP, 2 = REVERSE, 3 = RESUME
long end_motor_millis = 0;            ///< Variable to control the additional time added from entering the last section until the motor stops
long prev_millis_line_detection = 0;  ///< Variable to control time and avoid multiple detections of the same line
long prev_millis_front = 0;           ///< Variable to control time and avoid multiple detections of the wall from the front sensor
unsigned long rear_phase_until = 0;   ///< Variable to control time for the reverse system
int d_servo = 0;                      ///< How much the servo needs to move
unsigned long last_huskylens_request = 0; ///< Variable to control time for calling the Huskylens 2
int cam_correction = 0;               ///< Camera correction to be applied to the servo
int cam_count = 0;                    ///< Controls how many drive loops the camera correction has been applied
int cam_close = 0;                    ///< Controls how many drive loops the block reverse flag is up

/* FUNCTIONS */

/**
 * Request the demanded value of the indicated ToF Luna via I2C connectivity.
 * @param addr I2C address of the ToF Luna that you wish to request
 * @param reg Value to be requested. 0x00 for distance. 0x02 for strength
 * @return Desired value of the ToF Luna in question
 * @see LunaDistance()
 */
uint16_t LunaRead16(uint8_t addr, uint8_t reg) {
  Wire.beginTransmission(addr);                         // Begins I2C communication with the given address 
  Wire.write(reg);                                      // Tells ToF Luna that we desire the given type of information
  Wire.endTransmission(false);                          // Keeps the I2C communication active with the ToF Luna
  Wire.requestFrom(addr, (uint8_t)2);                   // Requests 2 bytes data from the ToF Luna. It releases the I2C bus after the request.
  if (Wire.available() < 2) return 0xFFFF;              // If less than 2 bytes retrieved returns 0xFFFF as failed
  return (uint16_t)(Wire.read() | (Wire.read() << 8));  // Returns the data
}

/**
 * This function returns the distance in mm measured by the requested 
 * Luna ToF and also ensures that this measurement makes sense using 
 * the strength of the Luna ToF, thus giving consistent results in 
 * borderline cases.
 * @param addr I2C address of the ToF Luna that you wish to request
 * @return Distance in mm measured
 * @return 0xFFFF if failed to measure
 * @see LunaRead16()
 */
uint16_t LunaDistance(uint8_t addr) {
  uint16_t d = LunaRead16(addr, 0x00);          // Request ToF Luna distance
  uint16_t strength = LunaRead16(addr, 0x02);   // Request ToF Luna strength
  if (d == 0xFFFF || strength == 0xFFFF || strength < LUNA_STRENGHT_MIN) return 0xFFFF; // Returns 0xFFFF if failed
  if (d == 0)                                   // The distance may be 0 because the sensor is too close to a wall and is saturated, or because it measures infinity
  {
    if (strength >= LUNA_CLOSE_STRENGTH) return LUNA_CLOSE_MM;  // If the strength is very high, the sensor is too close to the wall.
    return 1500;                                                // If the strength is very low, the sensor measures infinity.
  }
  return d*10;  // The ToF Luna returns cm, but the code needs mm
}

/**
 * Initialize HuskyLens communication (shares Wire1 with the TCS34725).
 * @param none
 * @return true if initialization successful
 * @return false if initialization was unseccessful
 * @see RequestHuskyLens()
 */
bool InitHuskyLens() {
  Wire1.setClock(100000);   // Wire1 is already initialized in setup() for the Adafruit TCS34275
  // Debug code in case it is not working the Huskylens 2
  if (!huskylens.begin(Wire1)) {
    Serial.println("ERROR: HuskyLens not detected on I2C (Wire1)");
    return false;
  }
  
  // Set algorithm to Color Recognition
  if (!huskylens.switchAlgorithm((eAlgorithm_t)ALGORITHM_COLOR_RECOGNITION)) {
    Serial.println("ERROR: Failed to set Color Recognition algorithm");
    return false;
  }
  
  Serial.println("HuskyLens initialized successfully");
  return true;
}

/**
 * Request color and position data from HuskyLens.
 * and picks the largest detected color block and 
 * computes a servo correction.
 * @param none
 * @return true if a valid green/red block was detected and correction worked properly
 * @return false if otherwise
 * @see InitHuskyLens()
 */
bool RequestHuskyLens() {

  // Refresh the result cache from HuskyLens
  huskylens.getResult((eAlgorithm_t)ALGORITHM_COLOR_RECOGNITION);

  // Check if there are results
  if (!huskylens.available((eAlgorithm_t)ALGORITHM_COLOR_RECOGNITION))
  {
    return false;
  }

  // Number of detected objects
  int count = huskylens.getCachedResultNum((eAlgorithm_t)ALGORITHM_COLOR_RECOGNITION);

  if (count <= 0) 
  {
    return false;
  }

  int bestIdx = -1;
  int maxArea = 0;
  uint8_t detected_color = 0;
  uint8_t detected_id = 0;

  for (int i = 0; i < count; i++) 
  {
    Result* result = huskylens.getCachedResultByIndex((eAlgorithm_t)ALGORITHM_COLOR_RECOGNITION, i);
    if (!result) continue;

    // Detect color ID
    uint8_t id = result->ID;
    uint8_t color = 0;
    if (id == HUSKYLENS_ID_GREEN_1 || id == HUSKYLENS_ID_GREEN_2) 
    {
      color = 1; // GREEN
    } 
    else if (id == HUSKYLENS_ID_RED_1 || id == HUSKYLENS_ID_RED_2) 
    {
      color = 2; // RED
    } 
    else 
    {
      continue;
    }

    // Check area
    int area = result->width * result->height;
    if (area <= 0) continue;

    // Choose the biggest object (closest)
    if (area > maxArea) 
    {
      maxArea = area;
      bestIdx = i;
      detected_id = id;
      detected_color = color;
    }
  }

  if (bestIdx == -1) 
  {
    return false;
  }

  // Get selected result
  Result* result = huskylens.getCachedResultByIndex((eAlgorithm_t)ALGORITHM_COLOR_RECOGNITION, bestIdx);

  if (!result) {
    return false;
  }

  // Get object position data
  int cx = result->xCenter;

  if (cx <= 0 || cx > 320) 
  {
    return false;
  }

  // Calculate servo correction
  if (detected_color == 1)      // Green, goes left
  {
    cam_correction = -((319 - cx) / CAM_GREEN_GAIN + 30);
  }
  else if (detected_color == 2) // Red, goes right
  {
    cam_correction = cx / CAM_RED_GAIN;
  }

  // Apply camera correction
  cam_count = CAM_COUNT_NUMBER;

  // ---------------------------------------------------------
  // Detect object too close
  // ---------------------------------------------------------

  int area = result->width * result->height;

  if (area >= CAM_CLOSE_AREA) 
  {
    cam_close = CAM_CLOSE_NUMBER;
  }

  return true;
}

/**
 * The driving, collision avoidance and obstacle-passing mechanism.
 * @see LunaDistance()
 * @see RequestHuskyLens()
 */
void Drive() {

  // Initialize variable for reading the ToF sensors
  static signed int distance_right, distance_left, distance_front;
  uint16_t d;

  //debug
  //distance_front = 1000000000;

  // Initialize variables for the camera information
  static int count_correction = 0;          // How many drive loops the camera correction has been applied
  static signed int correction = 0;         // Correction applied to the servo

  // Request HuskyLens information every 100 ms
  if (millis() - last_huskylens_request > 100)
  {
    RequestHuskyLens();
    last_huskylens_request = millis();
  }

  // It executes only if a color block has been detected
  // Saves the RequestHuskyLens() variables to local variables to this fuction
  if (cam_count > 0) 
  {
    count_correction = cam_count;     
    correction = cam_correction;      
    cam_count = 0;
  }

  // These lines read the ToF Luna sensors and save the distance 
  // in the corresponding variable as long as it hasn't failed reading.
  d = LunaDistance(LUNA_ADDR[0]);                                         // Right distance sensor
  if (d != 0xFFFF)
  {
    distance_right = d;
    if (distance_right > 1500) distance_right = 1500;                     // Limit to 1500mm
  }
  d = LunaDistance(LUNA_ADDR[1]);                                         // Left distance sensor
  if (d != 0xFFFF)
  {
    distance_left = d;
    if (distance_left > 1500) distance_left = 1500;                       // Limit to 1500mm
  }
  d = LunaDistance(LUNA_ADDR[2]);                                       // Front distance sensor
  if (d != 0xFFFF)
  {
    distance_front = d;
  }

  // If front sensor or Huskylens 2 detects an obstacle init rear sequence. This sequence is time based
  if (distance_front < FRONT_REAR_MM || cam_close > 0)
  {
    if (rear_phase == 0)
    {
      if ((prev_millis_front + 1200) <= millis())   // This if statement avoids multiple detection of the same wall
      {
        prev_millis_front = millis();
        rear_phase = 1;
        rear_phase_until = millis() + 250;
      }
    }
  }

  // Decay the camera "close" flag while the obstacle passes away
  if (cam_close > 0) cam_close--;

  // Rear sequence. This is time based
  if (rear_phase >= 1)
  {
    switch (rear_phase)
    {
      case 1:             // Stops the car for 250 ms (by default)
        travel_sense=0;
        if (millis() >= rear_phase_until){ rear_phase=2; rear_phase_until = millis() + 900; }
        break;
      case 2: 
        travel_sense=2;   // Reverse the car for 1500 ms (by default)
        if (millis() >= rear_phase_until){ rear_phase=3; rear_phase_until = millis() + 500; }
        break;
      case 3:             // The robot continues forward.
        travel_sense=1;
        rear_phase=0;
        break;
    }
  }

  // The servo needs to move a certain amount depending on the 
  // difference of distance measured between the left and 
  // the right ToF Luna sensors
  d_servo = (distance_right - distance_left)/10;

  // Limits the amount a servo can move in order to avoid collision of the wheels and the frame
  if (d_servo > 39) d_servo = 39;
  if (d_servo < -39) d_servo = -39;

  if (count_correction > 0)
  {
    d_servo = correction;
    count_correction--;
  }

  // In case of reverse, limited steering to avoid flipping
  if (rear_phase == 2)
  {                                 
    //if (d_servo > 40) d_servo = 12;
    //if (d_servo < -12) d_servo = -12;
    servo.write(-d_servo + 90);
  }
  else if (travel_sense == 1)
  {
    servo.write(d_servo + 90);
  }

  // Speed control
  int base_speed = BASE_SPEED;                    // Base speed of the robot

  if (distance_front < FRONT_REAR_MM || cam_close > 0)  // Reduces the speed before starting the reverse manoeuvre
  {
    base_speed = 120;
  }
  else if (distance_front < FRONT_BRAKE_MM)       // Reduces the speed when approaching a frontal wall
  {
    base_speed = 120;
  }

  if (d_servo >= 0)
  {
    ledcWrite(ENA_PIN, base_speed + d_servo);     // Sends the motor the speed. It is increased when turning
  }
  else 
  {
    ledcWrite(ENA_PIN, base_speed - d_servo);     // Sends the motor the speed. It is increased when turning
  }
}

/* SETUP AND LOOP FUNCTIONS */

/**
 * This code only runs once when the ESP32 starts up.
 * Initialize all systems and peripherals and wait for the 
 * start button to be pressed to start the program.
 * @param none
 * @return void
 */
void setup() {
  Serial.begin(115200);                           // Starts Serial for debugging reasons
  Wire.begin(SDA_PIN, SCL_PIN);                   // I2C communication for ToF Luna
  Wire.setTimeOut(100);
  Wire.setClock(100000);                          // ToF Luna at 100kHz
  Wire1.begin(SDA_PIN_COLOR, SCL_PIN_COLOR);      // I2C communication for TCS34725 color sensor and Huskylens 2
  
  servo.attach(SERVO_PIN);                        // Initialize Servo
  servo.write(90);                                // 0 position Servo

  // Pin Modes
  pinMode(BUTTON_PIN, INPUT_PULLUP);
  pinMode(MOTOR_A_PIN, OUTPUT);
  pinMode(MOTOR_B_PIN, OUTPUT);

  // Stop the motor
  digitalWrite(MOTOR_A_PIN, LOW);
  digitalWrite(MOTOR_B_PIN, LOW);

  ledcAttachChannel(ENA_PIN, 1000, 8, 2);         // PWM for the motor. Frequency = 1000, Resolution = 8, Channel = 2

  // FOR DEBUGGING
  // Checks ToF Luna presence and debug which ones don't work through the serial port.
  for (uint8_t i = 0; i < LUNA_COUNT; i++)
  {
    Wire.beginTransmission(LUNA_ADDR[i]);
    if (Wire.endTransmission() == 0)
    {
      Serial.print("TF-Luna ");
      Serial.print(i);
      Serial.print(" OK (0x");
      Serial.print(LUNA_ADDR[i], HEX);
      Serial.println(")");
    }
    else
    {
      Serial.print("TF-Luna ");
      Serial.print(i);
      Serial.print(" NOT found (0x");
      Serial.print(LUNA_ADDR[i], HEX);
      Serial.println(")");
    }
  }

  // Initialize color sensor. DEBUG through the serial port if not working.
  if (tcs.begin(0x29, &Wire1))
  {
    Serial.println("Found TCS34725 sensor");
  }
  else
  {
    Serial.println("WARNING: TCS34725 not detected, continuing without color.");
  }

  // Initialize HuskyLens
  if (!InitHuskyLens()) 
  {
    Serial.println("WARNING: HuskyLens init failed, continuing without vision.");
  }

  // Waits for START button to be pressed
  int countButton = 0;
  while (countButton <= 10)
  {
    button_state = digitalRead(BUTTON_PIN);
    if (button_state == LOW) countButton++;
    delay(10);
  }
}

/**
 * This code only runs all the time.
 * @param none
 * @return void
 */
void loop() {
  // Gets color temp from the Adafruit TCS34725 color sensor
  uint16_t r, g, b, c, colorTemp;                             // Initialize needed variables
  tcs.getRawData(&r, &g, &b, &c);                             // Gets the RGB and Clear channels
  colorTemp = tcs.calculateColorTemperature_dn40(r, g, b, c); // Calculates the color temperature from the RGBC channels

  // Increases corner count using the lines on the ground and the TCS34725 color sensor.
  if (colorTemp > 3000)
  {
    if ((prev_millis_line_detection + 700) <= millis())
    {
      prev_millis_line_detection = millis();
      corner_count++;
    }
  }

  // Stops the car when the number of corners is reached (12 corners)
  if (corner_count >= 12)
  {
    if ((end_motor_millis + 1500) <= millis())
    {
      travel_sense = 0;
    }
  }
  else
  {
    end_motor_millis = millis();
  }

  // Sets the travel sense. 0 = BRAKE, 1 = FORWARD, 2 = BACKWARD
  switch(travel_sense) {
    case 0:
      digitalWrite(MOTOR_A_PIN, LOW);
      digitalWrite(MOTOR_B_PIN, LOW);
      break;
    case 1:
      digitalWrite(MOTOR_A_PIN, HIGH);
      //digitalWrite(MOTOR_A_PIN, LOW);         // FOR DEBUGGING.
      digitalWrite(MOTOR_B_PIN, LOW);
      break;
    case 2:
      digitalWrite(MOTOR_A_PIN, LOW);
      digitalWrite(MOTOR_B_PIN, HIGH);
      //digitalWrite(MOTOR_B_PIN, LOW);         // FOR DEBUGGING.
      break;
  }

  Drive();        // The driving and collision avoidance algorithm
}
```

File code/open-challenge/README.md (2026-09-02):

# open-challenge.ino

# Introduction to the code

Although at first glance the code for the Open Challenge may seem trivial due to its apparent simplicity compared to the Obstacle Challenge, our goal with this code was not only to create something simple to quickly overcome this challenge, but also to create a foundation upon which to build the Obstacle Challenge code. With this idea in mind, our algorithm design and code structure have been designed to facilitate this transition.

On the other hand, we understand that the Open Challenge should demonstrate the minimum the robot is capable of, which is why we have also prioritized creating robust yet simple code.

# Code structure

All the code for this challenge is contained in a single .ino file, named open-challenge.ino. This code is executed in the robot's ESP32 main.

There are no other programs for this challenge.

We have not created any additional libraries or files as required.

# Algorithm design

A flowchart of the code's operation can be seen below.



As can be seen, as soon as the robot is powered on, it enters standby mode until the Start button is pressed. Meanwhile, as observed in the source code, the robot's various systems and peripherals are initialized (I2C communication, color sensor, servomotor, etc.).

Once the Start button is pressed, the robot enters the loop. We can divide the loop's operation into two parts:
1. Robot Movement
2. Limit Case Checking

## Robot movement

The strategy here is simple: keep the robot centered between the side walls at all times.

To achieve this, the Luna ToF sensors located on the sides of the robot measure the distance to the right and left. Then, using the difference between these distances, the servomotor is instructed to turn the wheels in the corresponding direction. For example, if the distance to the right is greater than to the left, the robot will turn its wheels to the right, and if the distance to the left is greater than to the right, the wheels will turn to the left. The benefit of using the difference in distances is that it allows the servomotor to turn only slightly if the difference is small, while if the difference is very large, it turns much more, allowing for better cornering.

With this, after testing, we have ensured that regardless of the direction of rotation, the starting position, or the size of the central square, the robot always remains centered.

## Check of limit cases

The loop also performs certain checks at all times on the following things, as shown in the flowchart:
- If the color sensor facing the ground detects the blue line, then the internal counter corner_count, which measures how many corners the robot has passed through, is incremented by one. This tells us how many sections the robot has traversed.
- If the front Luna ToF sensor measures a distance less than 350mm, the motor speed is reduced to avoid a collision. This can sometimes happen when getting too close to walls.
- If the front Luna ToF sensor measures a distance less than 150mm, a collision is practically imminent, and the reversing process is activated. This temporarily disables the robot's movement and makes it reverse to avoid getting stuck.
- If the corner_counter is equal to 12, the robot has already completed three laps and must stop in the final section.

# Bugs and errors found in the code

Throughout the development of this code, we encountered various problems and challenges that we had to resolve. This, in turn, allowed us to create a more robust code than we originally envisioned.

Initially, some minor problems we had included incorrectly assigning the I2C address to each Luna ToF sensor and missing resistors here and there. But above all, we would highlight the following problems we encountered, as their solution has improved the code's resilience, and we believe other users might encounter similar issues.

- One problem we found was that the Luna ToF sensors, when measuring very long distances (which we considered to be infinity), returned a measurement of 0 mm. On the other hand, when very close to a wall, since they weren't designed to measure such short distances, they also returned some erroneous values, highly variable, and in many cases, also 0 mm. This presented the problem of how to distinguish between 0 at a very long distance and 0 at a very short distance. For this, we used the "strength" data provided by the Luna ToF sensors themselves. After several tests, we verified that the strength was minimal when it was 0 at infinity and very high when it was 0 at very close range. Therefore, every time we obtained a value of 0, we performed a second check with the strength to determine what type of 0 it was. If it was 0 at infinity, we set it to 1500 mm.
- Sometimes, when the robot had to make very tight turns, it would pick up a lot of speed and crash into the walls. We originally designed a reversing mechanism that should have solved this problem. However, the frequency and manner of the collisions caused it to take a long time to complete the circuit, and in many cases, the reversing maneuver was ineffective. This was resolved by having the robot reduce its speed when it detects that it is approaching the walls. In many cases, this avoids the collision, and in those where it doesn't, the slower collision usually leaves the robot in a better position to more easily complete the circuit after reversing.

# Source code description

## Functions

| | Name |
| --- | --- |
| void IRAM_ATTR | **[OdometerInterrupt](#function-odometerinterrupt)**() |
| uint16_t | **[LunaRead16](#function-lunaread16)**(uint8_t addr, uint8_t reg) |
| uint16_t | **[LunaDistance](#function-lunadistance)**(uint8_t addr) |
| void | **[Drive](#function-drive)**() |
| void | **[ServoTurning](#function-servoturning)**(signed int _distance_right, signed int _distance_left) |
| void | **[setup](#function-setup)**() |
| void | **[loop](#function-loop)**() |

## Constants

| | Name | Value |
| --- | --- | --- |
| const uint8_t | **LUNA_COUNT** <br>Number of Luna time of flight sensors| 3
| const uint8_t[LUNA_COUNT] | **LUNA_ADDR** <br>I2C address of each ToF sensor. Right, Left, Front | {0x11, 0x12, 0x13} |
| const uint16_t | **LUNA_STRENGHT_MIN** <br>Minimum strenght needed from the ToF sensor to accept a measurement | 20 |
| const uint16_t | **LUNA_CLOSE_STRENGTH** <br>Minumum strength needed to consider a 0 distance measurement too close | 150 |
| const uint16_t | **LUNA_CLOSE_MM** <br>Value (mm) used in case of a too close measurement | 150 |
| const uint16_t | **FRONT_BRAKE_MM** <br>Progressive braking start distance (mm) threshold | 350 |
| const uint16_t | **FRONT_REAR_MM** <br>Reverse gear start distance (mm) threshold | 150 |
| const int | **MOTOR_B_PIN**  | 20 |
| const int | **MOTOR_A_PIN**  | 10 |
| const int | **ENA_PIN**  | 15 |
| const int | **BUTTON_PIN**  | 13 | 
| const int | **ODOMETER_PIN**  | 15 |
| const int | **SDA_PIN**  | 11 |
| const int | **SCL_PIN**  | 12 |
| const int | **SDA_PIN_COLOR**  | 40 |
| const int | **SCL_PIN_COLOR**  | 41 |
| const int | **SERVO_PIN**  | 9 |
| const int | **BASE_SPEED**  | 120 |

## Variables

| | Name |
| --- | --- |
| Adafruit_TCS34725 | **tcs** <br>Color sensor TCS34725 object.  |
| Servo | **servo** <br>Servo object.  |
| int | **button_state** <br>START button state.  |
| int | **corner_count** <br>Counts the number of corners the robot has passed. It should go from 0 to 12.  |
| long | **delay_line** <br>NOT IN USE.  |
| int | **travel_sense** <br>Controls travel sense. 0 = BRAKE, 1 = FORWARD, 2 = BACKWARD.  |
| byte | **rear_phase** <br>Controls the rear phases. 0 = NORMAL, 1 = STOP, 2 = REVERSE, 3 = RESUME.  |
| long | **end_motor_millis** <br>Variable to control the additional time added from entering the last section until the motor stops.  |
| long | **prev_millis_line_detection** <br>Variable to control time and avoid multiple detections of the same line.  |
| long | **prev_millis_front** <br>Variable to control time and avoid multiple detections of the wall from the front sensor.  |
| unsigned long | **rear_phase_until** <br>Variable to control time for the reverse system.  |
| long | **odo_filter** <br>Variable to control time and avoid multiple detections of the same step of the odometer.  |
| int | **odo_integral** <br>Odometer step count.  |
| int | **d_servo** <br>How much the servo needs to move.  |

## Functions Documentation

### function OdometerInterrupt

```cpp
void IRAM_ATTR OdometerInterrupt()
```

**Parameters**: 

  * **none** 

**Return**: void 

Odometer interrupt. It uses the ESP32 interrupt management system so that when the odometer moves, this code is executed.

--------------

### function LunaRead16

```cpp
uint16_t LunaRead16(uint8_t addr,uint8_t reg)
```

**Parameters**: 

  * **addr** I2C address of the ToF Luna that you wish to request 
  * **reg** Value to be requested. 0x00 for distance. 0x02 for strength 

**See**: [LunaDistance()](#function-lunadistance)

**Return**: Desired value of the ToF Luna in question 

Request the demanded value of the indicated ToF Luna via I2C connectivity. 

--------------

### function LunaDistance

```cpp
uint16_t LunaDistance(uint8_t addr)
```

**Parameters**: 

  * **addr** I2C address of the ToF Luna that you wish to request 

**See**: [LunaRead16()](#function-lunaread16)

**Return**: 

  * Distance in mm measured 
  * 0xFFFF if failed to measure 

This function returns the distance in mm measured by the requested Luna ToF and also ensures that this measurement makes sense using the strength of the Luna ToF, thus giving consistent results in borderline cases.

--------------

### function Drive

```cpp
void Drive()
```

**Parameters**: 

  * **none** 

**See**: 

  * [LunaDistance()](#function-lunadistance)
  * [ServoTurning()](#function-servoturning)

**Return**: void 

The driving and collision avoidance algorith. 

--------------

### function ServoTurning

```cpp
void ServoTurning(signed int _distance_right,signed int _distance_left)
```

**Parameters**: 

  * **_distance_right** The right distance measured by the ToF Luna sensor 
  * **_distance_left** The left distance measured by the ToF Luna sensor 

**See**: [Drive()](#function-drive)

**Return**: void 

The servo turning algorith. 

--------------

### function setup

```cpp
void setup()
```

**Parameters**: 

  * **none** 

**Return**: void 

This code only runs once when the ESP32 starts up. Initialize all systems and peripherals and wait for the start button to be pressed to start the program. 

--------------

### function loop

```cpp
void loop()
```

**Parameters**: 

  * **none** 

**Return**: void 

This code only runs all the time. 

## Source code

```cpp
/***********************************************************************
 *  FILE NAME:  open-challenge
 *
 *
 *  PURPOSE:    This program is the version of the main 
 *              robot code for the Open Challenge of the 
 *              Future Engineers category of the World
 *              Robot Olympiad.
 *  
 *
 *  HOW IT WORKS: The program uses side time-of-flight 
 *                distance sensors to keep the robot 
 *                constantly aligned with the center line 
 *                between the two side walls. Additionally, 
 *                in the event of a frontal collision or 
 *                when approaching a collision, the front 
 *                sensor is used to move backward or reduce 
 *                speed, respectively.
 *
 *
 *  LIBRARIES USED:
 *  Name                        Description
 *  ----                        -----------
 *  ESP32Servo                  Functions required to control a 
 *                               servomotor with the ESP32
 *  Wire                        Allows I2C communication
 *  Adafruit_TCS34725           Functions required to use the 
 *                               Adafruit TCS34725 RGB Color Sensor
 *
 *
 *  OTHER PROGRAMS NEEDED TO WORK
 *  Name                        Description
 *  ----                        -----------
 *  none
 *
 *
 *  CREATED BY: Vila-Stem 8
 *
 *                                                
 *  LAST MODIFIED: August 31st 2026                                     
 *                                                                      
 *                                                                      
 *  REPOSITORY: https://github.com/Vila-Stem/WRO_FUTURE_ENGINEERS_2026  
 *
 ***********************************************************************
*/

/* INCLUDE LIBRARIES */
#include <ESP32Servo.h>                                                   
#include <Wire.h>
#include <Adafruit_TCS34725.h>

/* CONSTANT VALUES */
/* Related to the Luna time of flight (ToF) sensor */
const uint8_t LUNA_COUNT = 3;                               ///< Number of Luna time of flight sensors
const uint8_t LUNA_ADDR[LUNA_COUNT] = {0x11, 0x12, 0x13};   ///< I2C address of each ToF sensor. Right, Left, Front
const uint16_t LUNA_STRENGHT_MIN = 20;                      ///< Minimum strenght needed from the ToF sensor to accept a measurement
const uint16_t LUNA_CLOSE_STRENGTH = 150;                   ///< Minumum strength needed to consider a 0 distance measurement too close
const uint16_t LUNA_CLOSE_MM = 150;                         ///< Value (mm) used in case of a too close measurement

/* Collision avoidance threshold distances */
const uint16_t FRONT_BRAKE_MM = 350;                        ///< Progressive braking start distance (mm) threshold
const uint16_t FRONT_REAR_MM = 150;                         ///< Reverse gear start distance (mm) threshold

/* Pins */
const int MOTOR_B_PIN = 20;
const int MOTOR_A_PIN = 10;
const int ENA_PIN = 15;                                     ///< Enabled motor pin. Used with PWM for speed control
const int BUTTON_PIN = 13; 
const int ODOMETER_PIN = 15; 
const int SDA_PIN = 11;
const int SCL_PIN = 12;
const int SDA_PIN_COLOR = 40;
const int SCL_PIN_COLOR = 41;
const int SERVO_PIN = 9;

const int BASE_SPEED = 120;

/* CREATE OBJECTS */
Adafruit_TCS34725 tcs = Adafruit_TCS34725(TCS34725_INTEGRATIONTIME_50MS, TCS34725_GAIN_60X);    ///< Color sensor TCS34725 object
Servo servo;                                                                                    ///< Servo object

/* VARIABLES */
int button_state = HIGH;              ///< START button state
int corner_count = 0;                 ///< Counts the number of corners the robot has passed. It should go from 0 to 12.
long delay_line = 0;                  ///< NOT IN USE
int travel_sense = 1;                 ///< Controls travel sense. 0 = BRAKE, 1 = FORWARD, 2 = BACKWARD
byte rear_phase = 0;                  ///< Controls the rear phases. 0 = NORMAL, 1 = STOP, 2 = REVERSE, 3 = RESUME
long end_motor_millis = 0;            ///< Variable to control the additional time added from entering the last section until the motor stops
long prev_millis_line_detection = 0;  ///< Variable to control time and avoid multiple detections of the same line
long prev_millis_front = 0;           ///< Variable to control time and avoid multiple detections of the wall from the front sensor
unsigned long rear_phase_until = 0;   ///< Variable to control time for the reverse system
long odo_filter = 0;                  ///< Variable to control time and avoid multiple detections of the same step of the odometer
int odo_integral = 0;                 ///< Odometer step count
int d_servo = 0;                      ///< How much the servo needs to move

/* FUNCTIONS */
/**
 * Odometer interrupt. It uses the ESP32 interrupt management 
 * system so that when the odometer moves, this code is executed.
 * @param none
 * @return void
 */
void IRAM_ATTR OdometerInterrupt(){
  if ((micros()-odo_filter)>1000)   // Avoids double detecting the same step
  {
    switch (travel_sense)
    {
      case 0:
        odo_integral++;
        break;
      case 1:
        odo_integral++;
        break;
      case 2:
        odo_integral--;
        break;
    }
    odo_filter = micros();
  }
}

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

/**
 * This function returns the distance in mm measured by the requested 
 * Luna ToF and also ensures that this measurement makes sense using 
 * the strength of the Luna ToF, thus giving consistent results in 
 * borderline cases.
 * @param addr I2C address of the ToF Luna that you wish to request
 * @return Distance in mm measured
 * @return 0xFFFF if failed to measure
 * @see LunaRead16()
 */
uint16_t LunaDistance(uint8_t addr) {
  uint16_t d = LunaRead16(addr, 0x00);          // Request ToF Luna distance
  uint16_t strength = LunaRead16(addr, 0x02);   // Request ToF Luna stregth
  if (d == 0xFFFF || strength == 0xFFFF || strength < LUNA_STRENGHT_MIN) return 0xFFFF; // Returns 0xFFFF if failed to measure or the strenght is too low
  if (d == 0)                                   // The distance may be 0 because the sensor is too close to a wall and is saturated, or because it measures infinity
  {
    if (strength >= LUNA_CLOSE_STRENGTH) return LUNA_CLOSE_MM;  // If the strength is very high, the sensor is too close to the wall.
    return 1500;                                                // If the strength is very low, the sensor measures infinity.
  }
  return d*10;  // The ToF Luna returns cm, but the code neeeds mm
}

/**
 * The driving and collision avoidance algorith.
 * @param none
 * @return void
 * @see LunaDistance()
 * @see ServoTurning()
 */
void Drive() 
{  
  // Initialize variable for reading the ToF sensors
  static signed int distance_right, distance_left, distance_front;
  uint16_t d;
  
  // These lines read the ToF Luna sensors and save the distance 
  // in the corresponding variable as long as it hasn't failed reading.
  d = LunaDistance(LUNA_ADDR[0]);                                         // Right distance sensor
  if (d != 0xFFFF) 
  {
    distance_right = d;
    if (distance_right > 1500) distance_right = 1500;                     // If the distance is greater than 1500mm, it limits it to 1500mm.
  }
  d = LunaDistance(LUNA_ADDR[1]);                                         // Left distance sensor
  if (d != 0xFFFF) 
  {
    distance_left = d;
    if (distance_left > 1500) distance_left = 1500;                       // If the distance is greater than 1500mm, it limits it to 1500mm.
  }
  d = LunaDistance(LUNA_ADDR[2]);                                         // Front distance sensor
  if (d != 0xFFFF) 
  {
    distance_front = d;
  }
  
  // If front sensor detects an obstacle init rear sequence. This sequence is time based
  if (distance_front < FRONT_REAR_MM)
  {
    if (rear_phase == 0)
    {
      if ((prev_millis_front + 1200) <= millis())   // This if statement avoids multiple detection of the same wall
      {
        prev_millis_front = millis();
        rear_phase = 1;
        rear_phase_until = millis() + 250;
      }
    }
  }

  // Rear sequence. This is time based
  if (rear_phase >= 1)
  {
    switch (rear_phase)
    {
      case 1:             // Stops the car for 250 mm (by deafult)
        travel_sense=0;
        if (millis() >= rear_phase_until){ rear_phase=2; rear_phase_until = millis() + 550; }
        break;
      case 2: 
        travel_sense=2;   // Reverse the car for 550 mm (by deafult)
        if (millis() >= rear_phase_until){ rear_phase=3; rear_phase_until = millis() + 50; }
        break;
      case 3:             // The robot continues forward.
        travel_sense=1;
        rear_phase=0;
        break;
    }
  }

  ServoTurning(distance_right, distance_left);    // Servo turning algorithm

  // Speed control
  int base_speed = BASE_SPEED;                    // Base speed of the robot

  if (distance_front < FRONT_REAR_MM)             // Reduces the speed before starting the reverse manouver
  {
    base_speed = 60;
  }
  else if (distance_front < FRONT_BRAKE_MM)       // Reduces the speed when approaching a frontal wall to avoid a collision or having to use the reverse manouver
  {
    base_speed = 75;
  }

  if (d_servo >= 0)
  {
    ledcWrite(ENA_PIN, base_speed + d_servo);     // Sends the motor the speed. It is increased when turning
  }
  else 
  {
    ledcWrite(ENA_PIN, base_speed - d_servo);     // Sends the motor the speed. It is increased when turning
  }
}

/**
 * The servo turning algorith.
 * @param _distance_right The right distance measured by the ToF Luna sensor
 * @param _distance_left The left distance measured by the ToF Luna sensor
 * @return void
 * @see Drive()
 */
void ServoTurning(signed int _distance_right, signed int _distance_left)
{
  // Initialize needed variables
  signed int distance_right = _distance_right;
  signed int distance_left = _distance_left;

  // The servo needs to move a certain amount depending on the 
  // difference of distance measured between the left and 
  // the right ToF Luna sensors
  d_servo = (distance_right - distance_left)/20;  

  // Limits the amount a servo can move in order to avoid collision of the wheels and the frame
  if (d_servo > 39) d_servo = 39;
  if (d_servo < -39) d_servo = -39;

  // In case of reverse, limited steering to avoid flipping
  if (rear_phase == 2)
  {                                 
    if (d_servo > 12) d_servo = 12;
    if (d_servo < -12) d_servo = -12;
    servo.write(-d_servo + 85);
  }
  else if (travel_sense == 1)
  {
    servo.write(d_servo + 85);
  }
}

/* SETUP AND LOOP FUNCTIONS */

/**
 * This code only runs once when the ESP32 starts up.
 * Initialize all systems and peripherals and wait for the 
 * start button to be pressed to start the program.
 * @param none
 * @return void
 */
void setup() {
  Serial.begin(115200);                             // Starts Serial for debugging reasons
  Wire.begin(SDA_PIN, SCL_PIN);                     // I2C communication for ToF Luna
  Wire.setTimeOut(100);
  Wire.setClock(100000);                            // ToF Luna at 100kHz                                                
  Wire1.begin(SDA_PIN_COLOR, SCL_PIN_COLOR);        // I2C communication for TCS34725 color sensor

  servo.attach(SERVO_PIN);                          // Initialize Servo
  servo.write(90);                                  // 0 postion Servo 
  
  // Pin Modes
  pinMode(BUTTON_PIN, INPUT_PULLUP);
  pinMode(MOTOR_A_PIN, OUTPUT);
  pinMode(MOTOR_B_PIN, OUTPUT);

  // Stop the motor
  digitalWrite(MOTOR_A_PIN, LOW);
  digitalWrite(MOTOR_B_PIN, LOW);

  ledcAttachChannel(ENA_PIN, 1000, 8, 2);           // PWM for the motor. Frequency = 1000, Resolution = 8, Channel = 2
  
  // FOR DEBUGGING
  // Checks ToF Luna presence and debug which ones don't work through the serial port.
  for (uint8_t i = 0; i < LUNA_COUNT; i++) 
  {
    Wire.beginTransmission(LUNA_ADDR[i]);
    if (Wire.endTransmission() == 0) 
    {
      Serial.print("TF-Luna ");
      Serial.print(i);
      Serial.print(" OK (0x");
      Serial.print(LUNA_ADDR[i], HEX);
      Serial.println(")");
    } 
    else 
    {
      Serial.print("TF-Luna ");
      Serial.print(i);
      Serial.print(" NOT found (0x");
      Serial.print(LUNA_ADDR[i], HEX);
      Serial.println(")");
    }
  }

  // Initialize color sensor. DEBUG trought the serial port if not working.
  if (tcs.begin(0x29, &Wire1)) 
  {                                           
    Serial.println("Found sensor");
  } 
  else 
  {
    Serial.println("WARNING: TCS34725 not detected, continuing without color.");
  }
  
  // Initialize odometer
  //attachInterrupt(ODOMETER_PIN, OdometerInterrupt,CHANGE);  // NOT IN USE

  // Waits for START button to be pressed
  int countButton = 0;
  while (countButton <= 10) 
  {
    button_state = digitalRead(BUTTON_PIN);
    if (button_state == LOW) countButton++;
    delay(10);
  }
}

/**
 * This code only runs all the time.
 * @param none
 * @return void
 */
void loop() {
  // Gets color temp from the Adafruit TCS34725 color sensor
  uint16_t r, g, b, c, colorTemp;                                 // Initialize needed variables
  tcs.getRawData(&r, &g, &b, &c);                                 // Gets the RGB and Clear channels
  colorTemp = tcs.calculateColorTemperature_dn40(r, g, b, c);     // Calculates the color temperature from the RGBC channels
  
  //Serial.print("Color Temp: "); Serial.println(colorTemp, DEC); // FOR DEBUGGING. Use it to calibrate the sensor

  // Increases corner count using the lines on the ground and the TCS34725 color sensor.
  if (colorTemp > 3000)
  {
    if ((prev_millis_line_detection + 700) <= millis())
    {
      prev_millis_line_detection = millis();
      corner_count++;
    }
  } 

  // Stops the car when the number of laps is reached (12 corners)
  if (corner_count >= 12) 
  {
    if ((end_motor_millis + 1500) <= millis()) 
    {
      travel_sense=0;    
    }
  } 
  else 
  {    
    end_motor_millis = millis();
  }

  // Sets the travel sense. 0 = BRAKE, 1 = FORWARD, 2 = BACKWARD
  switch(travel_sense)
  {
    case 0: 
      digitalWrite(MOTOR_A_PIN, LOW);
      digitalWrite(MOTOR_B_PIN, LOW);
      break;
    case 1: 
      //digitalWrite(MOTOR_A_PIN, LOW);     // FOR DEBUGGING.
      digitalWrite(MOTOR_A_PIN, HIGH);
      digitalWrite(MOTOR_B_PIN, LOW);
      break;
    case 2: 
      digitalWrite(MOTOR_A_PIN, LOW);
      //digitalWrite(MOTOR_B_PIN, LOW);     // FOR DEBUGGING.
      digitalWrite(MOTOR_B_PIN, HIGH);
      break;
  }
  
  Drive();        // The driving and collision avoidance algorith
}
```

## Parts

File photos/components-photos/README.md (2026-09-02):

# Components Photos

The components photos used for the README files and documentation.

| | |
| --- | --- |
|  |  |
|  |  |
|  |  |
|  |  |
|  |  |

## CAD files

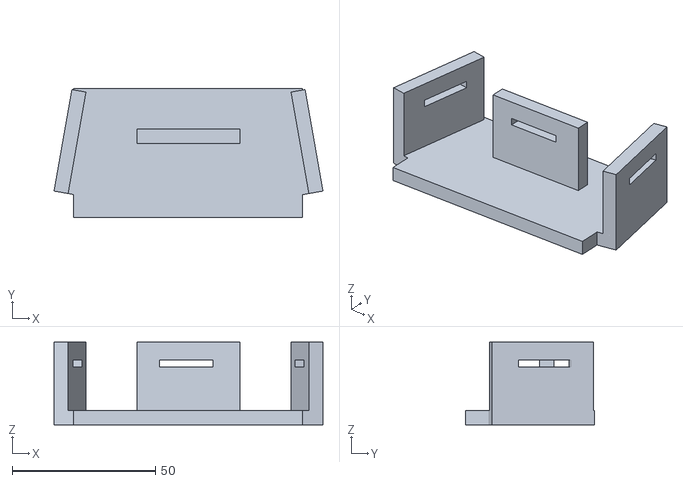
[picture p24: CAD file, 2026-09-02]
3d-designs/tf-luna-support.stl
94.0 x 45.0 x 29.0

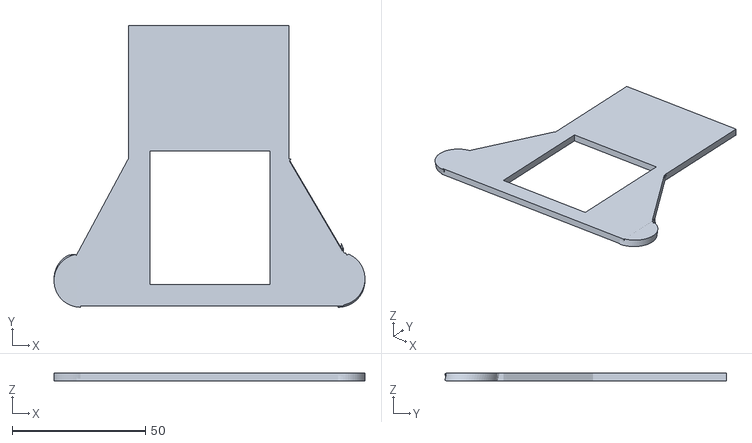
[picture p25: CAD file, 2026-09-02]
3d-designs/bumper.stl
116.5 x 105.5 x 3.00

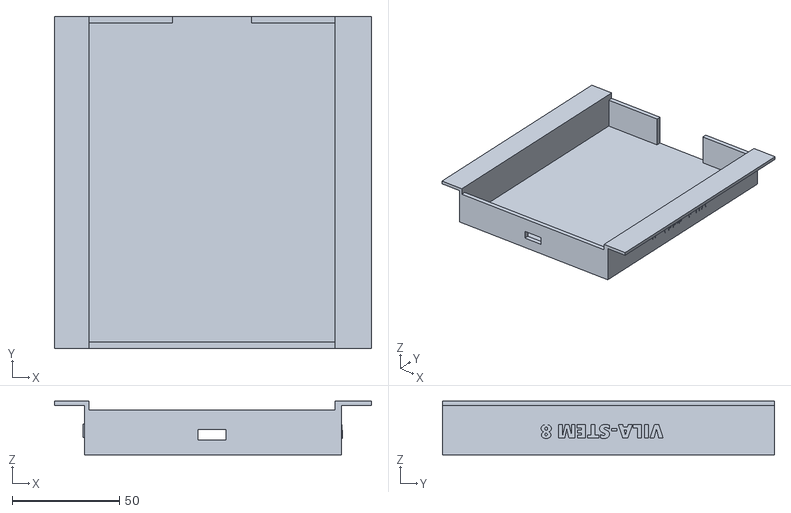
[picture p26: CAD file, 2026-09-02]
3d-designs/top-cover.stl
148.0 x 155.0 x 25.0

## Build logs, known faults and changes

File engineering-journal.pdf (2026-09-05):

# VILA-STEM 8

# ENGINEERING JOURNAL

## MADE FOR THE 2026 WRO

## FUTURE ENGINEERS COMPETITION

## LAST UPDATED: SEPTEMBER 1ST 2026

THE INFORMATION IN THIS DOCUMENT CAN ALSO BE FOUND IN THE OFFICIAL

REPOSITORY AT

https://github.com/Vila-Stem/WRO_FUTURE_ENGINEERS_2026

# Table of Contents

1 Introduction | 4
2 Mobility management | 6
3 Sensors and electricity | 9
4 Code | 21

2

TABLE OF CONTENTS | 3
5 Photos | 65
6 Videos | 69

### License

The code in this document is licensed under the GNU General Public License v3.0.

### Everything not under the GNU General Public License v3.0 in this document

### (including photographs, diagrams, etc) is under the Creative Commons

### Attribution Share Alike 4.0 International license

### 1CHAPTER

# Introduction

Vila-stem 8 is the Future Engineers team of the Vila-Stem educational robotics cultural associ-

ation, located in Vila-real, Spain. Some members of this team have already participated in the

WRO in different categories in previous years, including this year, while for others it is their first

time competing, but we are all equally excited to participate in the Future Engineers category of

WRO 2026.

Our first competition this season was the regional WRO in Dénia, where we won first place and

qualified for the national final.

Now we are heading to the national final of WRO Spain 2026 in Andorra, eager to present our

project.

Throughout this document, you will find an explanation of our robot and links to other docu-

ments that explain the different sections in more detail.

To comply with the competition rules, we have also included a Journal of Engineering in PDF

format. This document is a compilation of the information explained throughout this repository. 4

5


## Figure 1.1: Photo at our academy

### 2CHAPTER

# Mobility management

# 2.1 Chassis design


(a) Left image of the robot | (b) Right image of the robot

## Figure 2.1: Multiple images of the robot

The lower chassis base comes from a development kit we acquired, so we simply had to assemble

it. This kit provided the wheels, motor, and steering system, which simplified assembly. We

designed a top platform on top of this kit, where the components are installed, as well as another

set of parts to mount the components.

Purchasing this kit allowed us to have a metal chassis that better withstands the robot’s stresses.

This freed us up to design, using plastic and 3D printing, those parts that wouldn’t be subjected

to heavy loads.

6

2.2. HOW WE ARRIVED AT THIS DESIGN | 7

# 2.2 How we arrived at this design

Initially, the idea was to mount all the components on the lower chassis, but the lack of space and

the desire for a more aesthetically pleasing design led us to install a top platform. This platform

saves space and also provides easier access to the connections. We ruled out increasing the

robot’s height because this keeps the center of gravity low and maintains its compact size.

This year we also aimed for a more aesthetically pleasing robot, which is why the design includes,

for example, a decorative top cover and insulated cable covers, among other improvements.

# 2.3 Drive system


## Figure 2.2: Image of the motor mechanism. It can be seen the motor, the wheel axel and

## the gears

In our robot, the rear wheels are the drive wheels. There is a single axle connecting both wheels,

and a gear connects them directly to the motor, without using any differential mechanism. This

causes both wheels to always rotate at the same speed.

Although, theoretically, this mechanism could cause the wheels to slip on curves, since the path

of travel is different for each wheel in this case, we chose this system because it seemed sufficient

for our robot’s needs and is easier to install and maintain. A more complex mechanism would

have added an extra difficulty that, in the repeated tests we conducted, we didn’t find necessary

to implement. Any slippage does not affect the robot’s proper functioning.

During assembly, we encountered some problems. Some gears and parts didn’t fit together, and

it took us a while to get them all aligned, but we eventually managed.

8 | CHAPTER 2. MOBILITY MANAGEMENT

# 2.4 Steering system


## Figure 2.3: Image of the servo mechanism

The steering system is the typical pivot axle (like a wagon): the entire front axle rotates on a

central pin moved by the servo. It’s the most common system, but it works just as well and is

inexpensive, so it was the logical choice for us.

Here, too, we had problems, especially during assembly: some axle parts broke, and we had to

replace them with identical ones. There were also parts that were difficult to fit, some because

they weren’t very well made and others because we got a little confused during assembly.

Physically, there isn’t a stop that directly limits the servo’s movement. However, the code itself

includes limitations that would prevent the wheels from over-rotating and hitting the sides of

the chassis.

### 3CHAPTER

# Sensors and electricity

The robot requires components for both control and power, as well as for obtaining the neces-

sary information from the environment. This section will cover these components, why of their

selection, and connection.

Intentionally blank 9

10 | CHAPTER 3. SENSORS AND ELECTRICITY

# 3.1 List of sensors and electrical components

## 3.1.1 ESP32 S3

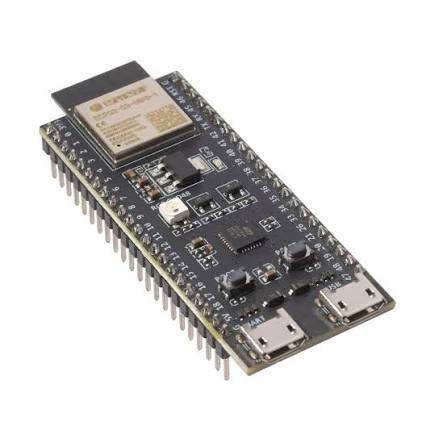
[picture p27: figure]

## Figure 3.1: Image of the ESP32 S3 microcontroller

### - WHY: We chose a variant of the ESP32 S3 that includes a camera connection port as the

### camera data processor. This microcontroller was selected because, being the same type as

### the main microcontroller, we could work more efficiently with both, only needing to be-

### come familiar with one variant. We have two microcontrollers because analyzing camera

### data is a very resource-intensive process, and therefore it was better to dedicate a mi-

### crocontroller to it. We selected the OV5640 from several cameras already available in the

classroom because it provided the best view of the track after testing all of them.

### - LOCATION: The microcontroller is located on the upper platform, beneath the top trim

### cover. The camera is mounted on a front bracket and connected to the microcontroller by

a cable.

### - VOLTAGE: 3.3V (can be powered via a 5V pin connected to a linear regulator)

### - CONNECTION TYPE: UART communication

3.1. LIST OF SENSORS AND ELECTRICAL COMPONENTS | 11

## 3.1.2 HUSKYLENS 2


## Figure 3.2: Image of the Huskylens 2

### - WHY: For much of the robot’s development, we tried using an ESP32 S3 CAM with a special

### lens. We originally chose this option because we thought it would be simpler than using

### a Huskylens 2, and because our experience with the Huskylens 1 had already been com-

### plicated. However, as development progressed, we realized it was actually much more

### complex. With the ESP32 S3 CAM, we had to manually calibrate several values per code

for it to detect colors, and the detection algorithms weren’t very effective. In contrast, after

some tests with the Huskylens 2, we saw that its ability to be calibrated using the built-in

### screen and button, along with its improved color detection algorithms, led us to choose

it. We had to adapt part of the obstacle code to this new sensor.

- LOCATION: It is located on the front of the robot, it has an special stand that keeps it

above the robot and looking with a small angle down.

### - VOLTAGE: 5V (can also be powered via 3.3V)

### - CONNECTION TYPE: I2C

12 | CHAPTER 3. SENSORS AND ELECTRICITY

## 3.1.3 L298N MOTOR DRIVER

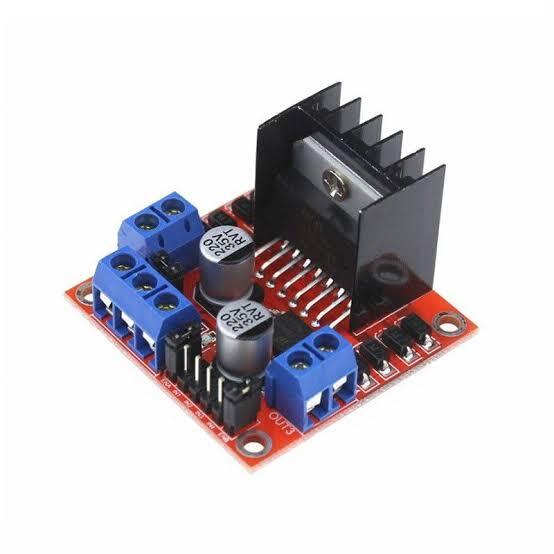
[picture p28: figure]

## Figure 3.3: Image of the L298N motor driver

- WHY: We chose this motor driver because we already had it in the classroom, it generally

### delivers good results, and it’s inexpensive and readily available should we need replace-

### ments. In the future, we would like to test the TB6612FNG, as we know it also offers good

### or even better results and takes up less space. In any case, the L298 motor has not pre-

sented any problems in all the tests performed and is easy to operate.

- LOCATION: It is located on the underside of the robot’s upper platform.

### - MOTOR VOLTAGE: 12V

### - LOGIC VOLTAGE: 5V (In our case, it is obtained through a linear regulator from the 12V

### motor voltage)

### - CONNECTION TYPE: PWM (speed control), 2 pins (to control the motor’s direction or

### brake)

3.1. LIST OF SENSORS AND ELECTRICAL COMPONENTS | 13

## 3.1.4 MOTOR


## Figure 3.4: Image of the 12V DC motor

### - WHY: This motor is a 12V DC motor. Initially, we tested it because it was the one we

### already had in class, and we wanted to avoid buying new motors if the one we already had

was working. It is true that this motor is somewhat bulky compared to other alternatives,

### but in previous, heavier projects, it never presented any torque or power problems, and

### the robot was already planned to be somewhat bulky, so we thought it would be a good

### option. The robot’s speed isn’t a major concern for us, as the time taken to complete the

challenges is low on the tie-breaking priority list in the rules.

- LOCATION: On the back of the robot’s lower platform.

### - VOLTAGE: 12V

## 3.1.5 TF-LUNA


## Figure 3.5: Image of the TF-Luna sensor

- WHY: To complete the missions, it’s essential to know the robot’s position relative to the

### walls. This requires considering the robot’s distance from the walls. There are several

### types of distance sensors: On the one hand, ultrasonic sensors are quite simple, inexpen-

14 | CHAPTER 3. SENSORS AND ELECTRICITY
| sive, and easy to find, but they offer low accuracy and vary significantly over long dis-
| tances, which caused us considerable problems in this same challenge last year. There-
| fore, we quickly ruled them out. Another option is to use Time-of-Flight (ToF) sensors.
| These sensors emit a beam of light and calculate the time between its emission, reflection,
| and return, allowing for precise determination of the distance to the reflected object, since
| the speed of light is constant. We noticed that many WRO projects use a rotating ToF sen-
| sor called LiDAR. After conducting some tests with a LiDAR we had and reading reviews
| from others who had worked with this sensor, we found it difficult to use, so we ruled out
| LiDAR. Finally, we selected fixed ToF sensors, the TF-Luna. The TF-Luna is relatively in-
| expensive, and after our initial testing, we found it to be quite accurate. Specifically, we
| tested it by measuring multiple distances between 5 cm and 3 m (dimensions designed
| for the Future Engineers challenge), and in every case, the distance obtained with the TF-
| Luna perfectly matched the physical measurement taken with a meter stick.
| • LOCATION: We have three sensors, one on each front side and one at the front. The side
| sensors are angled slightly forward. These sensors are mounted on a specially designed
| bracket and anchored to the lower platform.

### - VOLTAGE: 5V

### - CONNECTION TYPE: I2C

## 3.1.6 ADAFRUIT TCS34725


## Figure 3.6: Image of the Adafruit TCS34725 color sensor

### - WHY: To determine the robot’s position on the board and the number of sections tra-

### versed, we use orange lines conveniently placed at the corners of the board. We measure

### the robot’s movement over these lines using this color sensor. We chose this sensor after

finding positive online reviews and because it offered an I2C connection. Before using it,

we calibrated it, and after testing, we found it to be reliable and accurate, so we kept it.

- LOCATION: The lower platform has a hole facing the floor for the color sensor.

### - VOLTAGE: 3.3V

3.1. LIST OF SENSORS AND ELECTRICAL COMPONENTS | 15

### - CONNECTION TYPE: I2C

## 3.1.7 MG995 SERVOMOTOR

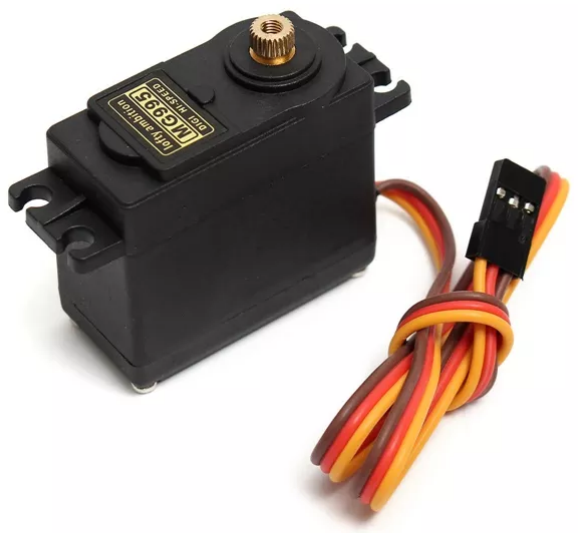
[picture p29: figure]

## Figure 3.7: Image of the MG995 servomotor

### - WHY: A servomotor is necessary to control the steering of the front wheels. This servo-

### motor was chosen because it offers higher torque (9.4 kg/cm) compared to other popular

options like the SG90 (1.8 kg/cm), while maintaining a relatively low price and good avail-

ability. Price is a particularly important factor in this case, as our experience competing in

### this category shows that servomotors tend to wear out considerably during training and

competition, requiring frequent replacement. Therefore, we prioritized a good price.

- LOCATION: On the lower platform.

### - VOLTAGE: 5V

### - CONNECTION TYPE: I2C

16 | CHAPTER 3. SENSORS AND ELECTRICITY

## 3.1.8 LM2596 CONVERTERS


## Figure 3.8: Image of the LM2596 converter

### - WHY: The 12V we get from the battery needs to be converted to 5V and 3.3V for the other

### components to function. This requires a converter. There are mainly two types: linear

### and switched-mode. Linear converters, like the LM7805, have the problem of being en-

ergy inefficient and generating a lot of heat when converting excess voltage. On the other

hand, switched-mode converters offer higher efficiency and generate less heat. Therefore,

### we selected a switched-mode voltage converter. The advantage of choosing this particu-

lar version of the LM2596 is that it is adjustable, which allows us to have several identical

converters in stock to meet the robot’s needs. It also has a display that shows the output

### voltage in real time, useful for monitoring the power status without needing a multime-

### ter. We have 2 12V to 5V converters because after installing the Huskylens 2 we saw that

### amount of current it used exceded the limits and made the voltage drop to the point that

### all the components connected to the only 5V converter stopped working, so we added one

12V to 5V only for the Huskylens 2 and another for all the rest of components.

- LOCATION: 2 are located on the underside of the robot’s upper platform and the Huskylens

2 5V converter is located on top of the robot’s upper platform.

3.1. LIST OF SENSORS AND ELECTRICAL COMPONENTS | 17

## 3.1.9 SWITCH


## Figure 3.9: Image of main power switch

- WHY: According to regulations, a switch is required to cut off or activate the robot’s power.
- LOCATION: On the side of the robot’s upper platform.

## 3.1.10 BUTTON

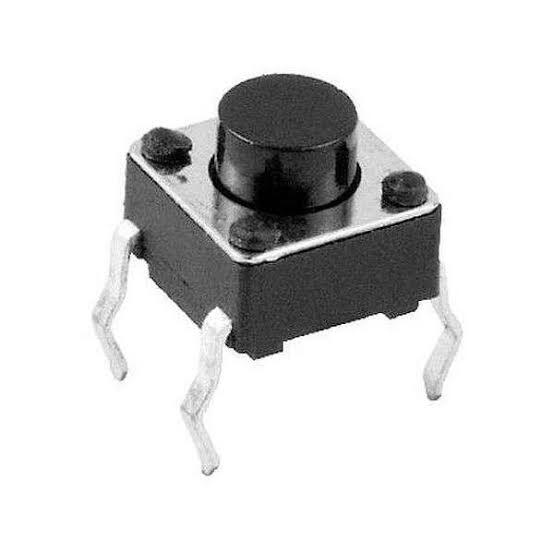
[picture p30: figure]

## Figure 3.10: Image of the start button

- WHY: According to regulations, a separate button is required to activate the robot’s exe-

cution of the challenge.

- LOCATION: On the robot’s upper platform.

18 | CHAPTER 3. SENSORS AND ELECTRICITY

# 3.2 Electrical diagram


## Figure 3.11: Robot electrical diagram showing all the different connections

3.3. CONNECTION TYPE DIAGRAM | 19

# 3.3 Connection type diagram

This diagram (fig. 3.12) shows the connection type of each component to the main microcon-

troller. The pink squares represent the microcontroller. The blue octagons are the sensors that

send information to the main microcontroller. The yellow circles are the actuators.


## Figure 3.12: This shows the connection type of each component

20 | CHAPTER 3. SENSORS AND ELECTRICITY

# 3.4 Power consumption

COMPONENT | VOLTAGE (V) | CURRENT (mA)
3 * LM2596 Converters | 12 | 50
Servomotor MG995 | 5 | ≈ 200 - 1200
Adafruit TCS34725 | 3.3 | 10
Motor | 12 | ≈ 300
3 * TF-Luna | 5 | 70
L298N Motor driver | Vm.: 12; Vlog.: 5 | 36
Huskylens 2 | 5 | ≈ 300 - 600
ESP32 S3 | 3.3 | ≈ 50

## Table 3.1: This table shows the consumption of each component

### 4CHAPTER

# Code

The following diagram (fig. 4.1) shows which code should be uploaded to the microcontroller in

each challenge.


## Figure 4.1: Which code should be uploaded to the microcontrollers in each challenge

21

22 | CHAPTER 4. CODE

### As we can see there are two programs: one for the Open Challenge and one for the Obstacle

Challenge, both uploaded to the only ESP32 S3.

In this chapter we will show how each code works, its functions and the source code.

Intentionally blank

4.1. OPEN-CHALLENGE.INO | 23

# 4.1 open-challenge.ino

## 4.1.1 Introduction to the code

Although at first glance the code for the Open Challenge may seem trivial due to its apparent

simplicity compared to the Obstacle Challenge, our goal with this code was not only to cre-

ate something simple to quickly overcome this challenge, but also to create a foundation upon

which to build the Obstacle Challenge code. With this idea in mind, our algorithm design and

code structure have been designed to facilitate this transition.

### On the other hand, we understand that the Open Challenge should demonstrate the minimum

the robot is capable of, which is why we have also prioritized creating robust yet simple code.

## 4.1.2 Code structure

All the code for this challenge is contained in a single .ino file, named open-challenge.ino. This

code is executed in the robot’s ESP32 main.

There are no other programs for this challenge.

We have not created any additional libraries or files as required.

## 4.1.3 Algorithm design

A flowchart of the code’s operation can be seen below (fig. 4.2).

As can be seen, as soon as the robot is powered on, it enters standby mode until the Start button

is pressed. Meanwhile, as observed in the source code, the robot’s various systems and periph-

erals are initialized (I2C communication, color sensor, servomotor, etc.).

Once the Start button is pressed, the robot enters the loop. We can divide the loop’s operation

### into two parts:

### 1. Robot Movement

### 2. Limit Case Checking

## 4.1.3.1 Robot movement

The strategy here is simple: keep the robot centered between the side walls at all times.

To achieve this, the Luna ToF sensors located on the sides of the robot measure the distance

to the right and left. Then, using the difference between these distances, the servomotor is in-

structed to turn the wheels in the corresponding direction. For example, if the distance to the

right is greater than to the left, the robot will turn its wheels to the right, and if the distance to the

24 | CHAPTER 4. CODE


## Figure 4.2: Open challenge algorith flowchart

4.1. OPEN-CHALLENGE.INO | 25

left is greater than to the right, the wheels will turn to the left. The benefit of using the difference

in distances is that it allows the servomotor to turn only slightly if the difference is small, while

if the difference is very large, it turns much more, allowing for better cornering.

With this, after testing, we have ensured that regardless of the direction of rotation, the starting

position, or the size of the central square, the robot always remains centered.

## 4.1.3.2 Check of limit cases

The loop also performs certain checks at all times on the following things, as shown in the

### flowchart:

- If the color sensor facing the ground detects the blue line, then the internal counter cor-

### ner_count, which measures how many corners the robot has passed through, is incre-

mented by one. This tells us how many sections the robot has traversed.

### - If the front Luna ToF sensor measures a distance less than 350mm, the motor speed is

reduced to avoid a collision. This can sometimes happen when getting too close to walls.

- If the front Luna ToF sensor measures a distance less than 150mm, a collision is practically

### imminent, and the reversing process is activated. This temporarily disables the robot’s

movement and makes it reverse to avoid getting stuck.

- If the corner_counter is equal to 12, the robot has already completed three laps and must

stop in the final section.

## 4.1.4 Bugs and errors found in the code

### Throughout the development of this code, we encountered various problems and challenges

that we had to resolve. This, in turn, allowed us to create a more robust code than we originally

envisioned.

Initially, some minor problems we had included incorrectly assigning the I2C address to each

Luna ToF sensor and missing resistors here and there. But above all, we would highlight the

following problems we encountered, as their solution has improved the code’s resilience, and

we believe other users might encounter similar issues.

### - One problem we found was that the Luna ToF sensors, when measuring very long dis-

### tances (which we considered to be infinity), returned a measurement of 0 mm. On the

### other hand, when very close to a wall, since they weren’t designed to measure such short

distances, they also returned some erroneous values, highly variable, and in many cases,

### also 0 mm. This presented the problem of how to distinguish between 0 at a very long dis-

tance and 0 at a very short distance. For this, we used the “strengt” data provided by the

### Luna ToF sensors themselves. After several tests, we verified that the strength was mini-

mal when it was 0 at infinity and very high when it was 0 at very close range. Therefore,

26 | CHAPTER 4. CODE
| every time we obtained a value of 0, we performed a second check with the strength to
| determine what type of 0 it was. If it was 0 at infinity, we set it to 1500 mm.
| • Sometimes, when the robot had to make very tight turns, it would pick up a lot of speed
| and crash into the walls. We originally designed a reversing mechanism that should have
| solved this problem. However, the frequency and manner of the collisions caused it to
| take a long time to complete the circuit, and in many cases, the reversing maneuver was
| ineffective. This was resolved by having the robot reduce its speed when it detects that
| it is approaching the walls. In many cases, this avoids the collision, and in those where
| it doesn’t, the slower collision usually leaves the robot in a better position to more easily

complete the circuit after reversing.

## 4.1.5 Functions

| Name
void IRAM_ATTR uint16_t uint16_t void void void void | OdometerInterrupt() LunaRead16(uint8_t addr, uint8_t reg) LunaDistance(uint8_t addr) Drive() ServoTurning(signed int _distance_right, signed int _distance_left) setup() loop()

## Table 4.1: Each function and its type

## 4.1.6 Constants

## Table 4.2: Each variable and its type

| Name | Value
const uint8_t const uint8_t[LUNA_COUNT] const uint16_t | LUNA_COUNT Number of Luna time of flight sensors LUNA_ADDR I2C address of each ToF sensor. Right, Left, Front LUNA_STRENGHT_MIN Minimum strenght needed from the ToF sensor to accept a measurement | 3 0x11, 0x12, 0x13 20

Continues on next page...

4.1. OPEN-CHALLENGE.INO | 27

## Table 4.2: Each variable and its type (continued)

### ... comes from previous page

Name | Value
const uint16_t | LUNA_CLOSE_STRENGTH

Minumum strength needed to

consider a 0 distance measurement

too close

150

const uint16_t | LUNA_CLOSE_MM
| Value (mm) used in case of a too
| close measurement

150

const uint16_t | FRONT_BRAKE_MM
| Progressive braking start
| distance (mm) threshold

350

const uint16_t | FRONT_REAR_MM
| Reverse gear start distance (mm)
| threshold

150

const int | MOTOR_B_PIN | 20
const int | MOTOR_A_PIN | 10
const int | ENA_PIN | 15
const int | BUTTON_PIN | 13
const int | ODOMETER_PIN | 15
const int | SDA_PIN | 11
const int | SCL_PIN | 12
const int | SDA_PIN_COLOR | 40
const int | SCL_PIN_COLOR | 41
const int | SERVO_PIN | 9
const int | BASE_SPEED | 120

## 4.1.7 Variables

## Table 4.3: Each variable and its type

| Name
Adafruit_TCS34725 Servo int int | tcs Color sensor TCS34725 object. servo Servo object. button_state START button state. corner_count Counts the number of corners the robot has passed. It should go from 0 to 12.

Continues on next page...

28 | CHAPTER 4. CODE

## Table 4.3: Each variable and its type (continued)

### ... comes from previous page

Name

long | delay_line

NOT IN USE.

int | travel_sense
Controls travel sense. | 0 = BRAKE, 1 = FORWARD,

2 = BACKWARD.

byte | rear_phase
Controls the rear phases. | 0 = NORMAL, 1 = STOP,

2 = REVERSE, 3 = RESUME.

long | end_motor_millis

Variable to control the additional time added

from entering the last section until the motor

stops.

long | prev_millis_line_detection

Variable to control time and avoid multiple

detections of the same line.

long | prev_millis_front

Variable to control time and avoid multiple

detections of the wall from the front sensor.

unsigned long | rear_phase_until

Variable to control time for the reverse system.

long | odo_filter

Variable to control time and avoid multiple

detections of the same step of the odometer.

int | odo_integral

Odometer step count.

int | d_servo

How much the servo needs to move.

## 4.1.8 Functions documentation

## 4.1.8.1 function OdometerInterrupt

1 | void IRAM_ATTR OdometerInterrupt ()

2

## Parameters: None

## Return: void

Odometer interrupt. It uses the ESP32 interrupt management system so that when the odometer

moves, this code is executed.

4.1. OPEN-CHALLENGE.INO | 29

## 4.1.8.2 function LunaRead16

1 | uint16_t LunaRead16 ( uint8_t addr , uint8_t reg )

2

## Parameters:

### - addr I2C address of the ToF Luna that you wish to request

### - reg Value to be requested. 0x00 for distance. 0x02 for strength

### Return: Desired value of the ToF Luna in question

Request the demanded value of the indicated ToF Luna via I2C connectivity.

## 4.1.8.3 function LunaDistance

1 | uint16_t LunaDistance ( uint8_t addr )

2

## Parameters:

### - addr I2C address of the ToF Luna that you wish to request

## Return:

### - Distance in mm measured

### - 0xFFFF if failed to measure

This function returns the distance in mm measured by the requested Luna ToF and also ensures

that this measurement makes sense using the strength of the Luna ToF, thus giving consistent

results in borderline cases.

## 4.1.8.4 function Drive

1 | void Drive ()

2

## Parameters: None

## Return: void

The driving and collision avoidance algorith.

30 | CHAPTER 4. CODE

## 4.1.8.5 function ServoTurning

1 | void ServoTurning ( signed int _distance_right , signed
| int _distance_left )

2

## Parameters:

### - _distance_right The right distance measured by the ToF Luna sensor

### - _distance_left The left distance measured by the ToF Luna sensor

## Return: void

The servo turning algorith.

## 4.1.8.6 function setup

1 | void setup ()

2

## Parameters: None

## Return: void

This code only runs once when the ESP32 starts up. Initialize all systems and peripherals and

wait for the start button to be pressed to start the program.

## 4.1.8.7 function loop

1 | void loop ()

2

## Parameters: None

## Return: void

This code only runs all the time.

## 4.1.9 Source code

1 | /* **************************************************************
2 | * | FILE NAME : | open - challenge
3 | *

4.1. OPEN-CHALLENGE.INO | 31
4 | *
5 | * | PURPOSE : | This program is the version of the main
6 | * | robot code for the Open Challenge of the
7 | * | Future Engineers category of the World
8 | * | Robot Olympiad .
9 | *
10 | *
11 | * | HOW IT WORKS : The program uses side time -of - flight
12 | * | distance sensors to keep the robot
13 | * | constantly aligned with the center line
14 | * | between the two side walls . Additionally ,
15 | * | in the event of a frontal collision or
16 | * | when approaching a collision , the front
17 | * | sensor is used to move backward or reduce
18 | * | speed , respectively .
19 | *
20 | *
21 | * | LIBRARIES USED :
22 | * | Name | Description
23 | * | ---- | -----------
24 | * | ESP32Servo | Functions required to control a
25 | * | servomotor with the ESP32
26 | * | Wire | Allows I2C communication
27 | * | Adafruit_TCS34725 | Functions required to use the
28 | * | Adafruit TCS34725 RGB Color Sensor
29 | *
30 | *
31 | * | OTHER PROGRAMS NEEDED TO WORK
32 | * | Name | Description
33 | * | ---- | -----------
34 | * | none
35 | *
36 | *
37 | * | CREATED BY: Vila - Stem 8
38 | *
39 | *
40 | * | LAST MODIFIED : August 31 st 2026
41 | *
42 | *
43 | * | REPOSITORY : https :// github . com/Vila - Stem /

WRO_FUTURE_ENGINEERS_2026

44 | *
45 | ***************************************************************
46 | */

47

48
49 | /* INCLUDE LIBRARIES */
50 | # include < ESP32Servo .h >
51 | # include < Wire .h >
52 | # include < Adafruit_TCS34725 .h >

53

32 | CHAPTER 4. CODE

54
55 | /* CONSTANT VALUES */
56 | /* Related to the Luna time of flight (ToF) sensor */
57 | const uint8_t LUNA_COUNT = 3; | /// <

Number of Luna time of flight sensors
58 | const uint8_t LUNA_ADDR [ LUNA_COUNT ] = {0 x11 , 0 x12 , 0 x13 }; | /// < I2C

address of each ToF sensor . Right , Left , Front
59 | const uint16_t LUNA_STRENGHT_MIN = 20; | /// <

Minimum strenght needed from the ToF sensor to accept a

measurement
60 | const uint16_t LUNA_CLOSE_STRENGTH = 150; | /// <

Minumum strength needed to consider a 0 distance measurement too

close
61 | const uint16_t LUNA_CLOSE_MM = 150; | /// <

Value (mm) used in case of a too close measurement

62
63 | /* Collision avoidance threshold distances */
64 | const uint16_t FRONT_BRAKE_MM = 350; | /// <

Progressive braking start distance (mm) threshold

65 | const uint16_t FRONT_REAR_MM = 150; | /// <

Reverse gear start distance (mm) threshold

66
67 | /* Pins */
68 | const int MOTOR_B_PIN = 20;
69 | const int MOTOR_A_PIN = 10;
70 | const int ENA_PIN = 15; | /// <

Enabled motor pin. Used with PWM for speed control

71 | const int BUTTON_PIN = 13;
72 | const int ODOMETER_PIN = 15;
73 | const int SDA_PIN = 11;
74 | const int SCL_PIN = 12;
75 | const int SDA_PIN_COLOR = 40;
76 | const int SCL_PIN_COLOR = 41;
77 | const int SERVO_PIN = 9;

78
79 const int BASE_SPEED = 120;

80

81
82 | /* CREATE OBJECTS */
83 | Adafruit_TCS34725 tcs = Adafruit_TCS34725 (
TCS34725_INTEGRATIONTIME_50MS , TCS34725_GAIN_60X ) ; | /// < Color

sensor TCS34725 object

84 Servo servo ;
/// < Servo object

85

86
87 | /* VARIABLES */
88 | int button_state = HIGH ; | /// < START button state
89 | int corner_count = 0; | /// < Counts the number of

corners the robot has passed . It should go from 0 to 12.
90 | long delay_line = 0; | /// < NOT IN USE

4.1. OPEN-CHALLENGE.INO | 33
91 | int travel_sense = 1; | /// < Controls travel sense . 0

= BRAKE , 1 = FORWARD , 2 = BACKWARD
92 | byte rear_phase = 0; | /// < Controls the rear phases .

0 = NORMAL , 1 = STOP , 2 = REVERSE , 3 = RESUME
93 | long end_motor_millis = 0; | /// < Variable to control the

additional time added from entering the last section until the

| motor stops
94 | long prev_millis_line_detection = 0; | /// < Variable to control time

and avoid multiple detections of the same line
95 | long prev_millis_front = 0; | /// < Variable to control time

and avoid multiple detections of the wall from the front sensor
96 | unsigned long rear_phase_until = 0; | /// < Variable to control time
| for the reverse system
97 | long odo_filter = 0; | /// < Variable to control time

and avoid multiple detections of the same step of the odometer
98 | int odo_integral = 0; | /// < Odometer step count
99 | int d_servo = 0; | /// < How much the servo needs
| to move

100

101
102 | /* FUNCTIONS */
103 | /**
104 | * Odometer interrupt . It uses the ESP32 interrupt management
105 | * system so that when the odometer moves , this code is executed .
106 | * @param none
107 | * @return void
108 | */
109 | void IRAM_ATTR OdometerInterrupt () {
110 | if (( micros () - odo_filter ) >1000) | // Avoids double detecting the
| same step
111 | {
112 | switch ( travel_sense )
113 | {
114 | case 0:
115 | odo_integral ++;
116 | break ;
117 | case 1:
118 | odo_integral ++;
119 | break ;
120 | case 2:
121 | odo_integral - -;
122 | break ;
123 | }
124 | odo_filter = micros () ;
125 | }
126 | }

127

128

129 | /**
130 | * Request the demanded value of the indicated ToF Luna via I2C
| connectivity .

34 | CHAPTER 4. CODE
131 | * @param addr I2C address of the ToF Luna that you wish to request
132 | * @param reg Value to be requested . 0 x00 for distance . 0 x02 for

strength

133 | * @return Desired value of the ToF Luna in question
134 | * @see LunaDistance ()
135 | */
136 | uint16_t LunaRead16 ( uint8_t addr , uint8_t reg ) {
137 | Wire . beginTransmission ( addr ) ; | // Begins

I2C communication with the given address
138 | Wire . write ( reg ) ; | // Tells ToF

Luna that we desire the given type of information
139 | Wire . endTransmission ( false ) ; | // Keeps the

I2C communication active with the ToF Luna
140 | Wire . requestFrom ( addr , ( uint8_t ) 2) ; | // Requests

2 bytes data from the ToF Luna . It releases the I2C bus after the

request .
141 | if ( Wire . available () < 2) return 0 xFFFF ; | // If less

than 2 bytes retrieved returns 0 xFFFF as failed
142 | return ( uint16_t ) ( Wire . read () | ( Wire . read () << 8) ) ; | // Returns

the data

143 }

144

145

146 | /**
147 | * This function returns the distance in mm measured by the

requested

148 | * Luna ToF and also ensures that this measurement makes sense using
149 | * the strength of the Luna ToF , thus giving consistent results in
150 | * borderline cases .
151 | * @param addr I2C address of the ToF Luna that you wish to request
152 | * @return Distance in mm measured
153 | * @return 0 xFFFF if failed to measure
154 | * @see LunaRead16 ()
155 | */
156 | uint16_t LunaDistance ( uint8_t addr ) {
157 | uint16_t d = LunaRead16 ( addr , 0 x00 ) ; | // Request ToF Luna

distance
158 | uint16_t strength = LunaRead16 ( addr , 0 x02 ) ; | // Request ToF Luna

stregth
159 if ( d == 0 xFFFF || strength == 0 xFFFF || strength < LUNA_STRENGHT_MIN ) return 0 xFFFF ; // Returns 0 xFFFF if failed to

measure or the strenght is too low
160 | if ( d == 0) | // The distance may

be 0 because the sensor is too close to a wall and is saturated ,

or because it measures infinity

161 | {
162 | if ( strength >= LUNA_CLOSE_STRENGTH ) return LUNA_CLOSE_MM ; | //

If the strength is very high , the sensor is too close to the wall

163 | return 1500; | //

If the strength is very low , the sensor measures infinity .

4.1. OPEN-CHALLENGE.INO | 35
164 | }
165 | return d *10; | // The ToF Luna returns cm , but the code neeeds mm
166 | }

167

168

169 | /**
170 | * The driving and collision avoidance algorith .
171 | * @param none
172 | * @return void
173 | * @see LunaDistance ()
174 | * @see ServoTurning ()
175 | */
176 | void Drive ()
177 | {
178 | // Initialize variable for reading the ToF sensors
179 | static signed int distance_right , distance_left , distance_front ;
180 | uint16_t d ;

181
182 | // These lines read the ToF Luna sensors and save the distance
183 | // in the corresponding variable as long as it hasn ’t failed
| reading .
184 | d = LunaDistance ( LUNA_ADDR [0]) ;

// Right distance sensor
185 | if ( d != 0 xFFFF )
186 | {
187 | distance_right = d ;
188 | if ( distance_right > 1500) distance_right = 1500;

// If the distance is greater than 1500 mm , it limits it to

| 1500 mm.
189 | }
190 | d = LunaDistance ( LUNA_ADDR [1]) ;

// Left distance sensor
191 | if ( d != 0 xFFFF )
192 | {
193 | distance_left = d ;
194 | if ( distance_left > 1500) distance_left = 1500;

// If the distance is greater than 1500 mm , it limits it to

| 1500 mm.
195 | }
196 | d = LunaDistance ( LUNA_ADDR [2]) ;

// Front distance sensor
197 | if ( d != 0 xFFFF )
198 | {
199 | distance_front = d ;
200 | }

201
202 // If front sensor detects an obstacle init rear sequence . This

sequence is time based
203 | if ( distance_front < FRONT_REAR_MM )
204 | {
205 | if ( rear_phase == 0)

36 | CHAPTER 4. CODE
206 | {
207 | if (( prev_millis_front + 1200) <= millis () ) | // This if

statement avoids multiple detection of the same wall

208 | {
209 | prev_millis_front = millis () ;
210 | rear_phase = 1;
211 | rear_phase_until = millis () + 250;
212 | }
213 | }
214 | }

215
216 | // Rear sequence . This is time based
217 | if ( rear_phase >= 1)
218 | {
219 | switch ( rear_phase )
220 | {
221 | case 1: | // Stops the car for 250 mm (by deafult )
222 | travel_sense =0;
223 | if ( millis () >= rear_phase_until ) { rear_phase =2;

rear_phase_until = millis () + 550; }

224 | break ;
225 | case 2:
226 | travel_sense =2; | // Reverse the car for 550 mm (by deafult )
227 | if ( millis () >= rear_phase_until ) { rear_phase =3;

rear_phase_until = millis () + 50; }

228 | break ;
229 | case 3: | // The robot continues forward .
230 | travel_sense =1;
231 | rear_phase =0;
232 | break ;
233 | }
234 | }

235
236 | ServoTurning ( distance_right , distance_left ) ; | // Servo turning

algorithm

237
238 | // Speed control
239 | int base_speed = BASE_SPEED ; | // Base speed of

the robot

240
241 | if ( distance_front < FRONT_REAR_MM ) | // Reduces the

speed before starting the reverse manouver

242 | {
243 | base_speed = 60;
244 | }
245 | else if ( distance_front < FRONT_BRAKE_MM ) | // Reduces the

speed when approaching a frontal wall to avoid a collision or

having to use the reverse manouver

246 | {
247 | base_speed = 75;
248 | }

4.1. OPEN-CHALLENGE.INO | 37

249
250 | if ( d_servo >= 0)
251 | {
252 | ledcWrite ( ENA_PIN , base_speed + d_servo ) ; | // Sends the motor
| the speed . It is increased when turning
253 | }
254 | else
255 | {
256 | ledcWrite ( ENA_PIN , base_speed - d_servo ) ; | // Sends the motor
| the speed . It is increased when turning
257 | }
258 | }

259

260

261 | /**
262 | * The servo turning algorith .
263 | * @param _distance_right The right distance measured by the ToF
| Luna sensor
264 | * @param _distance_left The left distance measured by the ToF Luna
| sensor
265 | * @return void
266 | * @see Drive ()
267 | */
268 | void ServoTurning ( signed int _distance_right , signed int
| _distance_left )
269 | {
270 | // Initialize needed variables
271 | signed int distance_right = _distance_right ;
272 | signed int distance_left = _distance_left ;

273
274 | // The servo needs to move a certain amount depending on the
275 | // difference of distance measured between the left and
276 | // the right ToF Luna sensors
277 | d_servo = ( distance_right - distance_left ) /20;

278
279 | // Limits the amount a servo can move in order to avoid collision
| of the wheels and the frame
280 | if ( d_servo > 39) d_servo = 39;
281 | if ( d_servo < -39) d_servo = -39;

282
283 | // In case of reverse , limited steering to avoid flipping
284 | if ( rear_phase == 2)
285 | {
286 | if ( d_servo > 12) d_servo = 12;
287 | if ( d_servo < -12) d_servo = -12;
288 | servo . write ( - d_servo + 85) ;
289 | }
290 | else if ( travel_sense == 1)
291 | {
292 | servo . write ( d_servo + 85) ;
293 | }

38 | CHAPTER 4. CODE
294 | }

295

296
297 /* SETUP AND LOOP FUNCTIONS */

298

299 | /**
300 | * This code only runs once when the ESP32 starts up.
301 | * Initialize all systems and peripherals and wait for the
302 | * start button to be pressed to start the program .
303 | * @param none
304 | * @return void
305 | */
306 | void setup () {
307 | Serial . begin (115200) ; | // Starts Serial
| for debugging reasons
308 | Wire . begin ( SDA_PIN , SCL_PIN ) ; | // I2C
| communication for ToF Luna
309 | Wire . setTimeOut (100) ;
310 | Wire . setClock (100000) ; | // ToF Luna at
| 100 kHz
311 | Wire1 . begin ( SDA_PIN_COLOR , SCL_PIN_COLOR ) ; | // I2C
| communication for TCS34725 color sensor

312
313 | servo . attach ( SERVO_PIN ) ; | // Initialize
| Servo
314 | servo . write (90) ; | // 0 postion
| Servo

315
316 | // Pin Modes
317 | pinMode ( BUTTON_PIN , INPUT_PULLUP ) ;
318 | pinMode ( MOTOR_A_PIN , OUTPUT ) ;
319 | pinMode ( MOTOR_B_PIN , OUTPUT ) ;

320
321 | // Stop the motor
322 | digitalWrite ( MOTOR_A_PIN , LOW ) ;
323 | digitalWrite ( MOTOR_B_PIN , LOW ) ;

324
325 | ledcAttachChannel ( ENA_PIN , 1000 , 8 , 2) ; | // PWM for the

motor . Frequency = 1000 , Resolution = 8 , Channel = 2

326
327 | // FOR DEBUGGING
328 | // Checks ToF Luna presence and debug which ones don ’t work
| through the serial port .
329 | for ( uint8_t i = 0; i < LUNA_COUNT ; i ++)
330 | {
331 | Wire . beginTransmission ( LUNA_ADDR [ i ]) ;
332 | if ( Wire . endTransmission () == 0)
333 | {
334 | Serial . print ("TF - Luna ") ;
335 | Serial . print ( i ) ;
336 | Serial . print (" OK (0x") ;

4.1. OPEN-CHALLENGE.INO | 39
337 | Serial . print ( LUNA_ADDR [ i ] , HEX ) ;
338 | Serial . println (")") ;
339 | }
340 | else
341 | {
342 | Serial . print ("TF - Luna ") ;
343 | Serial . print ( i ) ;
344 | Serial . print (" NOT found (0x") ;
345 | Serial . print ( LUNA_ADDR [ i ] , HEX ) ;
346 | Serial . println (")") ;
347 | }
348 | }

349
350 | // Initialize color sensor . DEBUG trought the serial port if not
| working .
351 | if ( tcs . begin (0 x29 , & Wire1 ) )
352 | {
353 | Serial . println (" Found sensor ") ;
354 | }
355 | else
356 | {
357 | Serial . println (" WARNING : TCS34725 not detected , continuing
| without color .") ;
358 | }

359
360 | // Initialize odometer
361 | // attachInterrupt ( ODOMETER_PIN , OdometerInterrupt , CHANGE ); | // NOT
| IN USE

362
363 | // Waits for START button to be pressed
364 | int countButton = 0;
365 | while ( countButton <= 10)
366 | {
367 | button_state = digitalRead ( BUTTON_PIN ) ;
368 | if ( button_state == LOW ) countButton ++;
369 | delay (10) ;
370 | }
371 | }

372

373

374 | /**
375 | * This code only runs all the time .
376 | * @param none
377 | * @return void
378 | */
379 | void loop () {
380 | // Gets color temp from the Adafruit TCS34725 color sensor
381 | uint16_t r , g , b , c , colorTemp ; | //
| Initialize needed variables
382 | tcs . getRawData (& r , &g , &b , & c ) ; | //
| Gets the RGB and Clear channels

40 | CHAPTER 4. CODE
383 | colorTemp = tcs . calculateColorTemperature_dn40 (r , g , b , c ) ; | //

Calculates the color temperature from the RGBC channels

384
385 // Serial . print (" Color Temp : "); Serial . println ( colorTemp , DEC); //

FOR DEBUGGING . Use it to calibrate the sensor

386
387 // Increases corner count using the lines on the ground and the

TCS34725 color sensor .
388 | if ( colorTemp > 3000)
389 | {
390 | if (( prev_millis_line_detection + 700) <= millis () )
391 | {
392 | prev_millis_line_detection = millis () ;
393 | corner_count ++;
394 | }
395 | }

396
397 | // Stops the car when the number of laps is reached (12 corners )
398 | if ( corner_count >= 12)
399 | {
400 | if (( end_motor_millis + 1500) <= millis () )
401 | {
402 | travel_sense =0;
403 | }
404 | }
405 | else
406 | {
407 | end_motor_millis = millis () ;
408 | }

409
410 | // Sets the travel sense . 0 = BRAKE , 1 = FORWARD , 2 = BACKWARD
411 | switch ( travel_sense )
412 | {
413 | case 0:
414 | digitalWrite ( MOTOR_A_PIN , LOW ) ;
415 | digitalWrite ( MOTOR_B_PIN , LOW ) ;
416 | break ;
417 | case 1:
418 | // digitalWrite ( MOTOR_A_PIN , LOW); | // FOR DEBUGGING .
419 | digitalWrite ( MOTOR_A_PIN , HIGH ) ;
420 | digitalWrite ( MOTOR_B_PIN , LOW ) ;
421 | break ;
422 | case 2:
423 | digitalWrite ( MOTOR_A_PIN , LOW ) ;
424 | // digitalWrite ( MOTOR_B_PIN , LOW); | // FOR DEBUGGING .
425 | digitalWrite ( MOTOR_B_PIN , HIGH ) ;
426 | break ;
427 | }

428
429 | Drive () ; | // The driving and collision avoidance algorith
430 | }

4.1. OPEN-CHALLENGE.INO | 41

431

Intentionally blank

42 | CHAPTER 4. CODE

# 4.2 obstacle-challenge.ino

## 4.2.1 Introduction to the code

We strongly recommend that you first study the code of the Open Challenge (Chapter 4.1) to

understand how the different functions work and then come to this chapter, because in order

not to unnecessarily repeat the explanations we will simplify those already explained.

## 4.2.2 Code structure

All the code for this challenge is contained in a single .ino file, named obstacle-challenge.ino.

This code is executed in the robot’s ESP32 main.

There are no other programs for this challenge.

We have not created any additional libraries or files as required.

## 4.2.3 Algorithm design

A flowchart of the code’s operation can be seen below (fig. 4.3).

As can be seen, as soon as the robot is powered on, it enters standby mode until the Start button

is pressed. Meanwhile, as observed in the source code, the robot’s various systems and periph-

erals are initialized (Huskylens 2, I2C communication, color sensor, servomotor, etc.).

Once the Start button is pressed, the robot enters the loop. We can divide the loop’s operation

### into three parts:

### 1. Robot Movement

### 2. Limit Case Checking

### 3. Camera analysis

## 4.2.3.1 Robot movement

The basic movement strategy is the same as in the Open Challenge: use the side TF-Luna sensors

to keep the robot as centered as possible between the side walls of the track. In fact, if the Ob-

stacle Challenge were to occur without any traffic signs, the robot would complete the challenge

in the same way as in the Open Challenge.

### Building on the foundation already explained, the sign avoidance mechanism is added. This

involves using information received from the camera (block type, position, etc.) and the block’s

X-axis position to add a correction to the servo’s rotation angle, depending on the block’s color.

For example, if a green block is encountered slightly to the right of the robot, a slight servo offset

4.2. OBSTACLE-CHALLENGE.INO | 43


## Figure 4.3: Obstacle challenge algorith flowchart

44 | CHAPTER 4. CODE

will be added so that the wheels turn a little more to the left than they would if there were no

block. Conversely, if a red block is encountered far to the right of the robot, a large offset will be

added so that the robot can avoid the blocks.

The basic strategy was already tested during the Open Challenge trials. The obstacle section

involved trial and error until it worked. The biggest problems we encountered were related to

the block detection mechanism, which we explain below, rather than the dodge mechanism.

## 4.2.3.2 Check of limit cases

The loop also performs certain checks at all times on the following things, as shown in the

### flowchart:

- If the color sensor facing the ground detects the blue line, then the internal counter cor-

### ner_count, which measures how many corners the robot has passed through, is incre-

mented by one. This tells us how many sections the robot has traversed.

### - If the front Luna ToF sensor measures a distance less than 350mm, the motor speed is

reduced to avoid a collision. This can sometimes happen when getting too close to walls.

- If the front Luna ToF sensor measures a distance less than 150mm, a collision is practically

### imminent, and the reversing process is activated. This temporarily disables the robot’s

movement and makes it reverse to avoid getting stuck.

- If the corner_counter is equal to 12, the robot has already completed three laps and must

stop in the final section.

## 4.2.3.3 Camera analysis

First, regarding the camera analysis, it’s worth noting that the Huskylens 2 wasn’t our first choice,

as explained in the electronics and sensors section. However, introducing the Huskylens 2 al-

lowed us to delegate some of the detection and calibration algorithms to those already integrated

into the camera, thus improving the code’s reliability and ease of use.

We utilize the Huskylens 2’s color detection algorithm, as it detects blocks of color, which is

precisely what we needed. The ESP32S3 constantly queries what the Huskylens 2 is seeing, ob-

taining certain data from each block it detects. Internally, we then select the largest block, which

will be the closest to the camera. This way, if it detects two signals, one near and one far, it first

acts on the nearer one.

Once the block is selected, we send its color and X position relative to the robot to the main code,

so the movement algorithm can handle the rest.

To calibrate the camera to the colors, we used the color training functionality already available

on the Huskylens 2, accessible via the screen and a button. In the various tests we conducted,

we found that compared to the Huskylens 1 (which we also had at the academy), the Huskylens

4.2. OBSTACLE-CHALLENGE.INO | 45

2 is much better at distinguishing colors and seeing the same color in different lighting environ-

ments. This is ideal because we cannot guarantee that the lighting will be constant across the

entire board on competition day, and this way, even if one part is brighter than another, it will

see the correct color in all cases.

## 4.2.4 Bugs and errors found in the code

In terms of movement, since we based our work on the already functional Open Challenge code,

we haven’t encountered any particular bugs. We recommend reviewing that section to see what

might be causing problems.

Some errors already related to this challenge include typical wiring mistakes, such as incorrectly

connecting the TX and RX pins. We’d like to highlight these main issues that bothered us the

### most:

### - One problem we observed after extensive testing is that the wheel servos wear out quite

### quickly, requiring frequent replacement. There’s no single solution, as wear is common

### with any machine; however, adapting to this wear is key. We’ve decided to purchase sev-

### eral spare servos to take with us to competitions. Furthermore, we’ve learned that if we

redesign the robot in the future, we should make servo replacement easier. Currently, it’s

a bit difficult, but we don’t have the time to redesign the entire mechanism.

- Another issue is that we originally used an ESP32 S3 CAM. This option is incredibly cheaper

than using the Huskylens 2; however, after using it for a while, we found that calibrating

it for our challenge was really difficult, since we had to manually manage nearly 10 values

for each color and then manually change them via code, which was very time-consuming.

### This, combined with the fact that the detection algorithm we set up wasn’t very good, led

us to opt for the Huskylens 2.

## 4.2.5 Functions

| Name
uint16_t uint16_t void bool bool void void | LunaRead16(uint8_t addr, uint8_t reg) LunaDistance(uint8_t addr) Drive() InitHuskyLens() RequestHuskyLens() setup() loop()

## Table 4.4: Each function and its type

46 | CHAPTER 4. CODE

## 4.2.6 Constants

## Table 4.5: Each variable and its type

Name | Value
const uint8_t | LUNA_COUNT

Number of Luna time of flight

sensors

3

const
uint8_t[LUNA_COUNT]

LUNA_ADDR

I2C address of each ToF sensor.

Right, Left, Front

0x11, 0x12, 0x13

const uint16_t | LUNA_STRENGHT_MIN
| Minimum strenght needed from the
| ToF sensor to accept a
| measurement

20

const uint16_t | LUNA_CLOSE_STRENGTH
| Minumum strength needed to
| consider a 0 distance measurement
| too close

150

const uint16_t | LUNA_CLOSE_MM
| Value (mm) used in case of a too
| close measurement

150

const uint16_t | FRONT_BRAKE_MM
| Progressive braking start
| distance (mm) threshold

350

const uint16_t | FRONT_REAR_MM
| Reverse gear start distance (mm)
| threshold

150

const int | MOTOR_B_PIN | 20
const int | MOTOR_A_PIN | 10
const int | ENA_PIN | 15
const int | BUTTON_PIN | 13
const int | ODOMETER_PIN | 15
const int | SDA_PIN | 11
const int | SCL_PIN | 12
const int | SDA_PIN_COLOR
| SDA for TCS34725 and HuskyLens 2 | 40
const int | SCL_PIN_COLOR
| SCL for TCS34725 and HuskyLens 2

41

const int | SERVO_PIN | 9
const int | BASE_SPEED | 120
const int | HUSKYLENS_ADDR
| HuskyLens 2 I2C address | 0x50

Continues on next page...

4.2. OBSTACLE-CHALLENGE.INO | 47

## Table 4.5: Each variable and its type (continued)

### ... comes from previous page

Name | Value
const int | HUSKYLENS_TIMEOUT_MS

Time it waits for HuskyLens

response

1000

const int | HUSKYLENS_ID_GREEN_1
| ID assigned to green in HuskyLens

1

const int | HUSKYLENS_ID_GREEN_2
| ID assigned to green in HuskyLens

3

const int | HUSKYLENS_ID_RED_1
| ID assigned to red in HuskyLens

2

const int | HUSKYLENS_ID_RED_2
| ID assigned to red in HuskyLens

4

const int | CAM_CLOSE_AREA
| Block area (width*height px) that
| means the object is too close and
| triggers reverse

90000

const int | CAM_COUNT_NUMBER
| How many drive loops the camera
| correction has to be applied

15

const int | CAM_CLOSE_NUMBER
| How many drive loops the block
| reverse flag has to be up

8

## 4.2.7 Variables

## Table 4.6: Each variable and its type

| Name
Adafruit_TCS34725 Servo int int long | tcs Color sensor TCS34725 object. servo Servo object. button_state START button state. corner_count Counts the number of corners the robot has passed. It should go from 0 to 12. delay_line NOT IN USE.

Continues on next page...

48 | CHAPTER 4. CODE

## Table 4.6: Each variable and its type (continued)

### ... comes from previous page

Name

int | travel_sense
Controls travel sense. | 0 = BRAKE, 1 = FORWARD,

2 = BACKWARD.

byte | rear_phase
Controls the rear phases. | 0 = NORMAL, 1 = STOP,

2 = REVERSE, 3 = RESUME.

long | end_motor_millis

Variable to control the additional time added

from entering the last section until the motor

stops.

long | prev_millis_line_detection

Variable to control time and avoid multiple

detections of the same line.

long | prev_millis_front

Variable to control time and avoid multiple

detections of the wall from the front sensor.

unsigned long | rear_phase_until

Variable to control time for the reverse system.

long | odo_filter

Variable to control time and avoid multiple

detections of the same step of the odometer.

int | odo_integral

Odometer step count.

int | d_servo

How much the servo needs to move.

## 4.2.8 Functions documentation

## 4.2.8.1 function LunaRead16

1 | uint16_t LunaRead16 ( uint8_t addr , uint8_t reg )

2

## Parameters:

### - addr I2C address of the ToF Luna that you wish to request

### - reg Value to be requested. 0x00 for distance. 0x02 for strength

### Return: Desired value of the ToF Luna in question

4.2. OBSTACLE-CHALLENGE.INO | 49

Request the demanded value of the indicated ToF Luna via I2C connectivity.

## 4.2.8.2 function LunaDistance

1 | uint16_t LunaDistance ( uint8_t addr )

2

## Parameters:

### - addr I2C address of the ToF Luna that you wish to request

## Return:

### - Distance in mm measured

### - 0xFFFF if failed to measure

This function returns the distance in mm measured by the requested Luna ToF and also ensures

that this measurement makes sense using the strength of the Luna ToF, thus giving consistent

results in borderline cases.

## 4.2.8.3 function InitHuskyLens

1 | bool InitHuskyLens ()

2

## Parameters: None

## Return:

### - true if initialization successful

### - false if initialization was unsuccessful

Initialize HuskyLens communication (shares Wire1 with the TCS34725).

## 4.2.8.4 function RequestHuskyLens()

1 | bool RequestHuskyLens ()

2

## Parameters: None

50 | CHAPTER 4. CODE

## Return:

### - true if a valid green/red block was detected

### - false if otherwise

Request color and position data from HuskyLens and picks the largest detected color block and

computes a servo correction.

## 4.2.8.5 function Drive

1 | void Drive ()

2

## Parameters: None

## Return: void

The driving and collision avoidance algorith.

## 4.2.8.6 function setup

1 | void setup ()

2

## Parameters: None

## Return: void

This code only runs once when the ESP32 starts up. Initialize all systems and peripherals and

wait for the start button to be pressed to start the program.

## 4.2.8.7 function loop

1 | void loop ()

2

## Parameters: None

## Return: void

This code only runs all the time.

4.2. OBSTACLE-CHALLENGE.INO | 51

## 4.2.9 Source code

1 | /* **************************************************************
2 | * | FILE NAME : | obstacle - challenge
3 | *
4 | *
5 | * | PURPOSE : | This program is the version of the main
6 | * | robot code for the Obstacle Challenge of the
7 | * | Future Engineers category of the World
8 | * | Robot Olympiad .
9 | *
10 | *
11 | * | HOW IT WORKS : The program uses side time -of - flight
12 | * | distance sensors to keep the robot
13 | * | constantly aligned with the center line
14 | * | between the two side walls . Additionally ,
15 | * | in the event of a frontal collision or
16 | * | when approaching a collision , the front
17 | * | sensor is used to move backward or reduce
18 | * | speed , respectively . It is connected to a
19 | * | HuskyLens 2 that tells if there is an object ,
20 | * | its position and color , so this code makes the
21 | * | servo turn enough to pass the obstacle through
22 | * | the right side .
23 | *
24 | *
25 | * | LIBRARIES USED :
26 | * | Name | Description
27 | * | ---- | -----------
28 | * | ESP32Servo | Functions required to control a
29 | * | servomotor with the ESP32
30 | * | Wire | Allows I2C communication
31 | * | Adafruit_TCS34725 | Functions required to use the
32 | * | Adafruit TCS34725 RGB Color Sensor
33 | * | DFRobot_HuskylensV2 | Functions for HuskyLens AI vision

sensor

34 | *
35 | *
36 | * | OTHER PROGRAMS NEEDED TO WORK
37 | * | Name | Description
38 | * | ---- | -----------
39 | * | none
40 | *
41 | *
42 | * | CREATED BY: Vila - Stem 8
43 | *
44 | * | LAST MODIFIED : August 31 st 2026
45 | *
46 | *
47 | * | REPOSITORY : https :// github . com/Vila - Stem /

WRO_FUTURE_ENGINEERS_2026

52 | CHAPTER 4. CODE
48 | *
49 | ***************************************************************
50 | */

51

52
53 | /* INCLUDE LIBRARIES */
54 | # include < ESP32Servo .h >
55 | # include < Wire .h >
56 | # include < Adafruit_TCS34725 .h >
57 | # include " DFRobot_HuskylensV2 .h"

58

59
60 | /* CONSTANT VALUES */
61 | /* Related to the Luna time of flight (ToF) sensor */
62 | const uint8_t LUNA_COUNT = 3; | /// <
| Number of Luna time of flight sensors
63 | const uint8_t LUNA_ADDR [ LUNA_COUNT ] = {0 x11 , 0 x12 , 0 x13 }; | /// < I2C
| address of each ToF sensor . Right , Left , Front
64 | const uint16_t LUNA_STRENGHT_MIN = 20; | /// <
| Minimum strenght needed from the ToF sensor to accept a
| measurement
65 | const uint16_t LUNA_CLOSE_STRENGTH = 150; | /// <

Minumum strength needed to consider a 0 distance measurement too

| close
66 | const uint16_t LUNA_CLOSE_MM = 150; | /// <
| Value (mm) used in case of a too close measurement

67
68 | /* Collision avoidance threshold distances */
69 | const uint16_t FRONT_BRAKE_MM = 350; | /// <
| Progressive braking start distance (mm) threshold
70 | const uint16_t FRONT_REAR_MM = 150; | /// <
| Reverse gear start distance (mm) threshold

71
72 | /* Pins */
73 | const int MOTOR_B_PIN = 20;
74 | const int MOTOR_A_PIN = 10;
75 | const int ENA_PIN = 15; | /// <
| Enabled motor pin. Used with PWM for speed control
76 | const int BUTTON_PIN = 13; | /// <
| START button pin
77 | const int SDA_PIN = 11;
78 | const int SCL_PIN = 12;
79 | const int SDA_PIN_COLOR = 40; | /// < SDA
| for TCS34725 and HuskyLens 2
80 | const int SCL_PIN_COLOR = 41; | /// < SCL
| for TCS34725 and HuskyLens 2
81 | const int SERVO_PIN = 9;

82
83 const int BASE_SPEED = 120;

84
85 /* Huskylens */

4.2. OBSTACLE-CHALLENGE.INO | 53
86 | const int HUSKYLENS_ADDR = 0 x50 ; | /// <
| HuskyLens 2 I2C address
87 | const int HUSKYLENS_TIMEOUT_MS = 1000; | /// <

Time it waits for HuskyLens response
88 | const int HUSKYLENS_ID_GREEN_1 = 1; | /// < ID
| assigned to green in HuskyLens
89 | const int HUSKYLENS_ID_GREEN_2 = 3; | /// < ID
| assigned to green in HuskyLens
90 | const int HUSKYLENS_ID_RED_1 = 2; | /// < ID
| assigned to red in HuskyLens
91 | const int HUSKYLENS_ID_RED_2 = 4; | /// < ID
| assigned to red in HuskyLens
92 | const int CAM_CLOSE_AREA = 90000; | /// <

Block area ( width * height px) that means the object is too close

| and triggers reverse
93 | const int CAM_COUNT_NUMBER = 15; | /// < How

many drive loops the camera correction has to be applied
94 | const int CAM_CLOSE_NUMBER = 8; | /// < How

many drive loops the block reverse flag has to be up
95 | // ALGORITHM_COLOR_RECOGNITION is defined by the HuskyLens library
96 | // ( value 4). This guard is only a safety net for library versions
97 | // that do not expose it.
98 | # ifndef ALGORITHM_COLOR_RECOGNITION
99 | # define ALGORITHM_COLOR_RECOGNITION 4
100 | # endif

101

102
103 | /* CREATE OBJECTS */
104 | Adafruit_TCS34725 tcs = Adafruit_TCS34725 (
TCS34725_INTEGRATIONTIME_50MS , TCS34725_GAIN_60X ) ;
105 | Servo servo ;
106 | HuskylensV2 huskylens ;

107

108
109 | /* VARIABLES */
110 | int button_state = HIGH ; | /// < START button state
111 | int corner_count = 0; | /// < Counts the number of

corners the robot has passed . It should go from 0 to 12.
112 | long delay_line = 0; | /// < NOT IN USE
113 | int travel_sense = 1; | /// < Controls travel sense . 0
| = BRAKE , 1 = FORWARD , 2 = BACKWARD
114 | byte rear_phase = 0; | /// < Controls the rear phases .

0 = NORMAL , 1 = STOP , 2 = REVERSE , 3 = RESUME
115 | long end_motor_millis = 0; | /// < Variable to control the

additional time added from entering the last section until the

| motor stops
116 | long prev_millis_line_detection = 0; | /// < Variable to control time

and avoid multiple detections of the same line
117 | long prev_millis_front = 0; | /// < Variable to control time

and avoid multiple detections of the wall from the front sensor
118 | unsigned long rear_phase_until = 0; | /// < Variable to control time

54 | CHAPTER 4. CODE

for the reverse system
119 | int d_servo = 0; | /// < How much the servo needs

to move
120 unsigned long last_huskylens_request = 0; /// < Variable to control

time for calling the Huskylens 2
121 | int cam_correction = 0; | /// < Camera correction to be

applied to the servo
122 | int cam_count = 0; | /// < Controls how many drive

loops the camera correction has been applied
123 | int cam_close = 0; | /// < Controls how many drive

loops the block reverse flag is up

124

125
126 /* FUNCTIONS */

127

128 | /**
129 | * Request the demanded value of the indicated ToF Luna via I2C

connectivity .

130 | * @param addr I2C address of the ToF Luna that you wish to request
131 | * @param reg Value to be requested . 0 x00 for distance . 0 x02 for

strength

132 | * @return Desired value of the ToF Luna in question
133 | * @see LunaDistance ()
134 | */
135 | uint16_t LunaRead16 ( uint8_t addr , uint8_t reg ) {
136 | Wire . beginTransmission ( addr ) ; | // Begins

I2C communication with the given address
137 | Wire . write ( reg ) ; | // Tells ToF

Luna that we desire the given type of information
138 | Wire . endTransmission ( false ) ; | // Keeps the

I2C communication active with the ToF Luna
139 | Wire . requestFrom ( addr , ( uint8_t ) 2) ; | // Requests

2 bytes data from the ToF Luna . It releases the I2C bus after the

request .
140 | if ( Wire . available () < 2) return 0 xFFFF ; | // If less

than 2 bytes retrieved returns 0 xFFFF as failed
141 | return ( uint16_t ) ( Wire . read () | ( Wire . read () << 8) ) ; | // Returns

the data

142 }

143

144

145 | /**
146 | * This function returns the distance in mm measured by the

requested

147 | * Luna ToF and also ensures that this measurement makes sense using
148 | * the strength of the Luna ToF , thus giving consistent results in
149 | * borderline cases .
150 | * @param addr I2C address of the ToF Luna that you wish to request
151 | * @return Distance in mm measured
152 | * @return 0 xFFFF if failed to measure
153 | * @see LunaRead16 ()

4.2. OBSTACLE-CHALLENGE.INO | 55
154 | */
155 | uint16_t LunaDistance ( uint8_t addr ) {
156 | uint16_t d = LunaRead16 ( addr , 0 x00 ) ; | // Request ToF Luna

distance
157 | uint16_t strength = LunaRead16 ( addr , 0 x02 ) ; | // Request ToF Luna

strength
158 if ( d == 0 xFFFF || strength == 0 xFFFF || strength < LUNA_STRENGHT_MIN ) return 0 xFFFF ; // Returns 0 xFFFF if failed
159 | if ( d == 0) | // The distance may

be 0 because the sensor is too close to a wall and is saturated ,

or because it measures infinity

160 | {
161 | if ( strength >= LUNA_CLOSE_STRENGTH ) return LUNA_CLOSE_MM ; | //

If the strength is very high , the sensor is too close to the wall

162 | return 1500; | //

If the strength is very low , the sensor measures infinity .

163 | }
164 | return d *10; | // The ToF Luna returns cm , but the code needs mm
165 | }

166

167

168 | /**
169 | * Initialize HuskyLens communication ( shares Wire1 with the
TCS34725 ).
170 | * @param none
171 | * @return true if initialization successful
172 | * @return false if initialization was unseccessful
173 | * @see RequestHuskyLens ()
174 | */
175 | bool InitHuskyLens () {
176 | Wire1 . setClock (100000) ; | // Wire1 is already initialized in setup
() for the Adafruit TCS34275
177 | // Debug code in case it is not working the Huskylens 2
178 | if (! huskylens . begin ( Wire1 ) ) {
179 | Serial . println (" ERROR : HuskyLens not detected on I2C ( Wire1 )") ;
180 | return false ;
181 | }

182
183 | // Set algorithm to Color Recognition
184 | if (! huskylens . switchAlgorithm (( eAlgorithm_t )
ALGORITHM_COLOR_RECOGNITION ) ) {
185 | Serial . println (" ERROR : Failed to set Color Recognition algorithm
") ;
186 | return false ;
187 | }

188
189 | Serial . println (" HuskyLens initialized successfully ") ;
190 | return true ;
191 | }

192

56 | CHAPTER 4. CODE

193

194 | /**
195 | * Request color and position data from HuskyLens .
196 | * and picks the largest detected color block and
197 | * computes a servo correction .
198 | * @param none
199 | * @return true if a valid green / red block was detected
200 | * @return false if otherwise
201 | * @see InitHuskyLens ()
202 | */
203 | bool RequestHuskyLens () {
204 | // Refresh the result cache from the sensor
205 | huskylens . getResult (( eAlgorithm_t ) ALGORITHM_COLOR_RECOGNITION ) ;

206
207 | // Check if there are results available for the color recognition
| algorithm
208 | if (! huskylens . available (( eAlgorithm_t ) ALGORITHM_COLOR_RECOGNITION
) )
209 | {
210 | return false ;
211 | }

212
213 | // How many color objects are being detected
214 | int count = huskylens . getCachedResultNum (( eAlgorithm_t )
| ALGORITHM_COLOR_RECOGNITION ) ;
215 | if ( count <= 0)
216 | {
217 | return false ;
218 | }

219
220 | // Find the largest block (the closest one)
221 | int bestIdx = -1;
222 | int maxArea = 0;
223 | for (int i = 0; i < count ; i ++)
224 | {
225 | Result * result = huskylens . getCachedResultByIndex (( eAlgorithm_t )
ALGORITHM_COLOR_RECOGNITION , i ) ; | // Gets the result data of each
| block by calling it by its ID number
226 | if ( result )
227 | {
228 | int area = result - > width * result - > height ; | //
| Calculates the block area ( width * height )
229 | if ( area > maxArea ) | //
| Checks if the area of this block is bigger than the max. area
230 | {
231 | maxArea = area ; | //
| Saves the biggest area detected
232 | bestIdx = i ; | //
| Saves the ID number of the biggest area detected
233 | }
234 | }

4.2. OBSTACLE-CHALLENGE.INO | 57
235 | }
236 | if ( bestIdx == -1) | //

Checks that the " find largest block " system did not failed

237 | {
238 | return false ;
239 | }

240
241 | // Gets the result data of the biggest area block
242 | Result * result = huskylens . getCachedResultByIndex (( eAlgorithm_t )
ALGORITHM_COLOR_RECOGNITION , bestIdx ) ;
243 | if (! result )
244 | {
245 | return false ;
246 | }

247
248 // Map HuskyLens learned color ID to our color scheme (1 = GREEN , 2 = RED)
249 | int color = 0;
250 | if ( result - > ID == HUSKYLENS_ID_GREEN_1 || result - > ID ==
HUSKYLENS_ID_GREEN_2 )
251 | {
252 | color = 1; | // GREEN
253 | }
254 | else if ( result - > ID == HUSKYLENS_ID_RED_1 || result - > ID ==
HUSKYLENS_ID_RED_2 )
255 | {
256 | color = 2; | // RED
257 | }
258 | else
259 | {
260 | return false ; // Unknown color . Failed .
261 | }

262
263 // HuskyLens returns x center (0 left side of the camera screen ,

320 right side of the camera screen )

264 | int cx = result - > xCenter ;
265 | int area = result - > width * result - > height ;
266 | if ( cx <= 0 || cx > 320) | // Validate detection making sure it

is between the allowed values

267 | {
268 | return false ;
269 | }

270
271 | // Calculate correction
272 | if ( color == 1) | // GREEN , negative correction to go left
273 | {
274 | cam_correction = -((320 - cx ) / 6) ;
275 | }
276 | else if ( color == 2) | // RED , positive correction to go right
277 | { // RED
278 | cam_correction = cx / 6;

58 | CHAPTER 4. CODE
279 | }

280
281 cam_count = CAM_COUNT_NUMBER ;

282
283 | // Detects if a block is too close to the camera and the ToF Luna
| frontal sensor has not seen it.
284 | // It uses the area of the block to know if it is too big and has
| to start the reverse manouver .
285 | if ( area >= CAM_CLOSE_AREA )
286 | {
287 | cam_close = CAM_CLOSE_NUMBER ;
288 | }

289
290 | // Debug output
291 | const char * colorName = ( color == 1) ? " GREEN " : " RED";
292 | Serial . printf (" HUSKYLENS : color =%s cx =%d area =%d corr =%d\n",
| colorName , cx , area , cam_correction ) ;

293
294 | // Retuns true if everything worked properly
295 | return true ;
296 | }

297

298

299 | /**
300 | * The driving , collision avoidance and obstacle - passing mechanism .
301 | * @see LunaDistance ()
302 | * @see RequestHuskyLens ()
303 | */
304 | void Drive () {

305
306 | // Initialize variable for reading the ToF sensors
307 | static signed int distance_right , distance_left , distance_front ;
308 | uint16_t d ;

309

310 | // debug
311 | distance_front = 1000000000;

312
313 | // Initialize variables for the camera information
314 | static int count_correction = 0; | // How many drive loops
| the camera correction has been applied
315 | static signed int correction = 0; | // Correction applied to
| the servo

316
317 | // Request HuskyLens information every 100 ms
318 | if ( millis () - last_huskylens_request > 100)
319 | {
320 | RequestHuskyLens () ;
321 | last_huskylens_request = millis () ;
322 | }

323
324 // It executes only if a color block has been detected

4.2. OBSTACLE-CHALLENGE.INO | 59
325 | // Saves the RequestHuskyLens () variables to local variables to

this fuction
326 | if ( cam_count > 0)
327 | {
328 | count_correction = cam_count ;
329 | correction = cam_correction ;
330 | cam_count = 0;
331 | }

332
333 | // These lines read the ToF Luna sensors and save the distance
334 | // in the corresponding variable as long as it hasn ’t failed
| reading .
335 | d = LunaDistance ( LUNA_ADDR [0]) ;
| // Right distance sensor
336 | if ( d != 0 xFFFF )
337 | {
338 | distance_right = d ;
339 | if ( distance_right > 1500) distance_right = 1500;
| // Limit to 1500 mm
340 | }
341 | d = LunaDistance ( LUNA_ADDR [1]) ;
| // Left distance sensor
342 | if ( d != 0 xFFFF )
343 | {
344 | distance_left = d ;
345 | if ( distance_left > 1500) distance_left = 1500;
| // Limit to 1500 mm
346 | }
347 | /*d = LunaDistance ( LUNA_ADDR [2]) ;
| // Front distance sensor
348 | if (d != 0 xFFFF )
349 | {
350 | distance_front = d;
351 | }*/

352
353 | // If front sensor or Huskylens 2 detects an obstacle init rear
| sequence . This sequence is time based
354 | if ( distance_front < FRONT_REAR_MM || cam_close > 0)
355 | {
356 | if ( rear_phase == 0)
357 | {
358 | if (( prev_millis_front + 1200) <= millis () ) | // This if

statement avoids multiple detection of the same wall

359 | {
360 | prev_millis_front = millis () ;
361 | rear_phase = 1;
362 | rear_phase_until = millis () + 250;
363 | }
364 | }
365 | }

366

60 | CHAPTER 4. CODE
367 | // Decay the camera " close " flag while the obstacle passes away
368 | if ( cam_close > 0) cam_close - -;

369
370 | // Rear sequence . This is time based
371 | if ( rear_phase >= 1)
372 | {
373 | switch ( rear_phase )
374 | {
375 | case 1: | // Stops the car for 250 ms (by default )
376 | travel_sense =0;
377 | if ( millis () >= rear_phase_until ) { rear_phase =2;

rear_phase_until = millis () + 1500; }

378 | break ;
379 | case 2:
380 | travel_sense =2; | // Reverse the car for 1500 ms (by default
)
381 | if ( millis () >= rear_phase_until ) { rear_phase =3;

rear_phase_until = millis () + 500; }

382 | break ;
383 | case 3: | // The robot continues forward .
384 | travel_sense =1;
385 | rear_phase =0;
386 | break ;
387 | }
388 | }

389
390 | // The servo needs to move a certain amount depending on the
391 | // difference of distance measured between the left and
392 | // the right ToF Luna sensors
393 | d_servo = ( distance_right - distance_left ) /10;

394
395 // Limits the amount a servo can move in order to avoid collision

of the wheels and the frame
396 | if ( d_servo > 39) d_servo = 39;
397 | if ( d_servo < -39) d_servo = -39;

398
399 | if ( count_correction > 0)
400 | {
401 | d_servo = correction ;
402 | count_correction - -;
403 | }

404
405 | // In case of reverse , limited steering to avoid flipping
406 | if ( rear_phase == 2)
407 | {
408 | // if ( d_servo > 40) d_servo = 12;
409 | // if ( d_servo < -12) d_servo = -12;
410 | servo . write ( - d_servo + 90) ;
411 | }
412 | else if ( travel_sense == 1)
413 | {

4.2. OBSTACLE-CHALLENGE.INO | 61
414 | servo . write ( d_servo + 90) ;
415 | }

416
417 | // Speed control
418 | int base_speed = BASE_SPEED ; | // Base speed of

the robot

419
420 | if ( distance_front < FRONT_REAR_MM || cam_close > 0) | // Reduces

the speed before starting the reverse manoeuvre

421 | {
422 | base_speed = 120;
423 | }
424 | else if ( distance_front < FRONT_BRAKE_MM ) | // Reduces the

speed when approaching a frontal wall

425 | {
426 | base_speed = 120;
427 | }

428
429 | if ( d_servo >= 0)
430 | {
431 | ledcWrite ( ENA_PIN , base_speed + d_servo ) ; | // Sends the motor

the speed . It is increased when turning

432 | }
433 | else
434 | {
435 | ledcWrite ( ENA_PIN , base_speed - d_servo ) ; | // Sends the motor

the speed . It is increased when turning

436 | }
437 | }

438

439
440 /* SETUP AND LOOP FUNCTIONS */

441

442 | /**
443 | * This code only runs once when the ESP32 starts up.
444 | * Initialize all systems and peripherals and wait for the
445 | * start button to be pressed to start the program .
446 | * @param none
447 | * @return void
448 | */
449 | void setup () {
450 | Serial . begin (115200) ; | // Starts Serial

for debugging reasons
451 | Wire . begin ( SDA_PIN , SCL_PIN ) ; | // I2C

communication for ToF Luna
452 | Wire . setTimeOut (100) ;
453 | Wire . setClock (100000) ; | // ToF Luna at 100

kHz
454 | Wire1 . begin ( SDA_PIN_COLOR , SCL_PIN_COLOR ) ; | // I2C

communication for TCS34725 color sensor and Huskylens 2

455

62 | CHAPTER 4. CODE
456 | servo . attach ( SERVO_PIN ) ; | // Initialize
| Servo
457 | servo . write (90) ; | // 0 position
| Servo

458
459 | // Pin Modes
460 | pinMode ( BUTTON_PIN , INPUT_PULLUP ) ;
461 | pinMode ( MOTOR_A_PIN , OUTPUT ) ;
462 | pinMode ( MOTOR_B_PIN , OUTPUT ) ;

463
464 | // Stop the motor
465 | digitalWrite ( MOTOR_A_PIN , LOW ) ;
466 | digitalWrite ( MOTOR_B_PIN , LOW ) ;

467
468 | ledcAttachChannel ( ENA_PIN , 1000 , 8 , 2) ; | // PWM for the

motor . Frequency = 1000 , Resolution = 8 , Channel = 2

469
470 | // FOR DEBUGGING
471 | // Checks ToF Luna presence and debug which ones don ’t work
| through the serial port .
472 | for ( uint8_t i = 0; i < LUNA_COUNT ; i ++)
473 | {
474 | Wire . beginTransmission ( LUNA_ADDR [ i ]) ;
475 | if ( Wire . endTransmission () == 0)
476 | {
477 | Serial . print ("TF - Luna ") ;
478 | Serial . print ( i ) ;
479 | Serial . print (" OK (0x") ;
480 | Serial . print ( LUNA_ADDR [ i ] , HEX ) ;
481 | Serial . println (")") ;
482 | }
483 | else
484 | {
485 | Serial . print ("TF - Luna ") ;
486 | Serial . print ( i ) ;
487 | Serial . print (" NOT found (0x") ;
488 | Serial . print ( LUNA_ADDR [ i ] , HEX ) ;
489 | Serial . println (")") ;
490 | }
491 | }

492
493 | // Initialize color sensor . DEBUG through the serial port if not
| working .
494 | if ( tcs . begin (0 x29 , & Wire1 ) )
495 | {
496 | Serial . println (" Found TCS34725 sensor ") ;
497 | }
498 | else
499 | {
500 | Serial . println (" WARNING : TCS34725 not detected , continuing
| without color .") ;

4.2. OBSTACLE-CHALLENGE.INO | 63
501 | }

502
503 | // Initialize HuskyLens
504 | if (! InitHuskyLens () )
505 | {
506 | Serial . println (" WARNING : HuskyLens init failed , continuing
| without vision .") ;
507 | }

508
509 | // Waits for START button to be pressed
510 | int countButton = 0;
511 | while ( countButton <= 10)
512 | {
513 | button_state = digitalRead ( BUTTON_PIN ) ;
514 | if ( button_state == LOW ) countButton ++;
515 | delay (10) ;
516 | }
517 | }

518

519

520 | /**
521 | * This code only runs all the time .
522 | * @param none
523 | * @return void
524 | */
525 | void loop () {
526 | // Gets color temp from the Adafruit TCS34725 color sensor
527 | uint16_t r , g , b , c , colorTemp ; | //
| Initialize needed variables
528 | tcs . getRawData (& r , &g , &b , & c ) ; | //
| Gets the RGB and Clear channels
529 | colorTemp = tcs . calculateColorTemperature_dn40 (r , g , b , c ) ; //
| Calculates the color temperature from the RGBC channels

530
531 | // Increases corner count using the lines on the ground and the
| TCS34725 color sensor .
532 | if ( colorTemp > 3000)
533 | {
534 | if (( prev_millis_line_detection + 700) <= millis () )
535 | {
536 | prev_millis_line_detection = millis () ;
537 | corner_count ++;
538 | }
539 | }

540
541 // Stops the car when the number of corners is reached (12 corners )
542 | if ( corner_count >= 12)
543 | {
544 | if (( end_motor_millis + 1500) <= millis () )
545 | {

64 | CHAPTER 4. CODE
546 | travel_sense = 0;
547 | }
548 | }
549 | else
550 | {
551 | end_motor_millis = millis () ;
552 | }

553
554 | // Sets the travel sense . 0 = BRAKE , 1 = FORWARD , 2 = BACKWARD
555 | switch ( travel_sense ) {
556 | case 0:
557 | digitalWrite ( MOTOR_A_PIN , LOW ) ;
558 | digitalWrite ( MOTOR_B_PIN , LOW ) ;
559 | break ;
560 | case 1:
561 | digitalWrite ( MOTOR_A_PIN , HIGH ) ;
562 | // digitalWrite ( MOTOR_A_PIN , LOW); | // FOR DEBUGGING .
563 | digitalWrite ( MOTOR_B_PIN , LOW ) ;
564 | break ;
565 | case 2:
566 | digitalWrite ( MOTOR_A_PIN , LOW ) ;
567 | digitalWrite ( MOTOR_B_PIN , HIGH ) ;
568 | // digitalWrite ( MOTOR_B_PIN , LOW); | // FOR DEBUGGING .
569 | break ;
570 | }

571
572 | Drive () ; | // The driving and collision avoidance algorithm
573 | }

574

### 5CHAPTER

# Photos

# 5.1 Robot photos

Several photos of our robot from different angles.


## Figure 5.1: Front image

65

66 | CHAPTER 5. PHOTOS

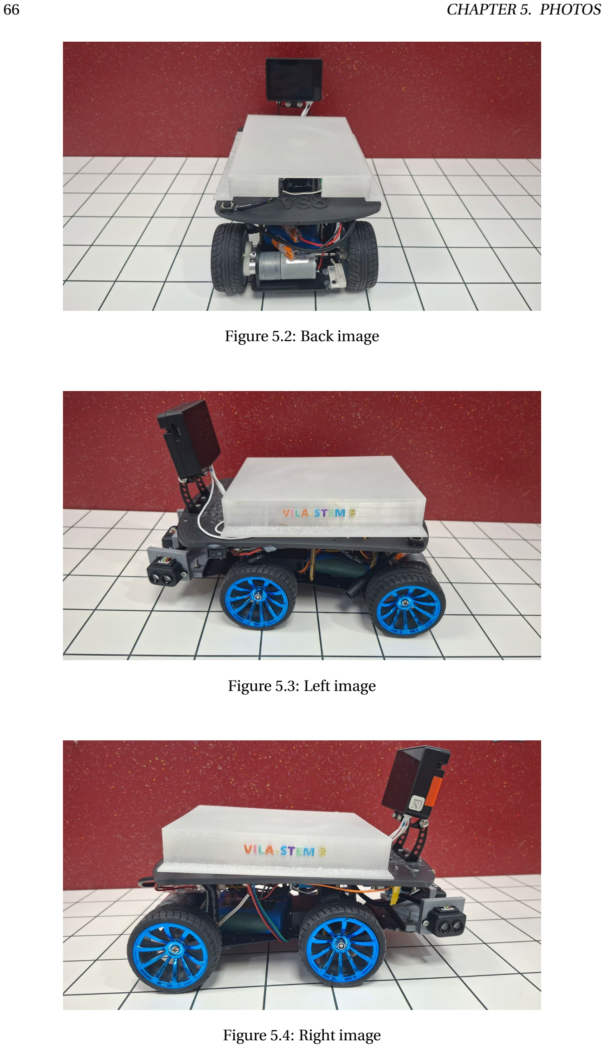
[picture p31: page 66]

## Figure 5.2: Back image

## Figure 5.3: Left image

## Figure 5.4: Right image

5.1. ROBOT PHOTOS | 67


## Figure 5.5: Top image

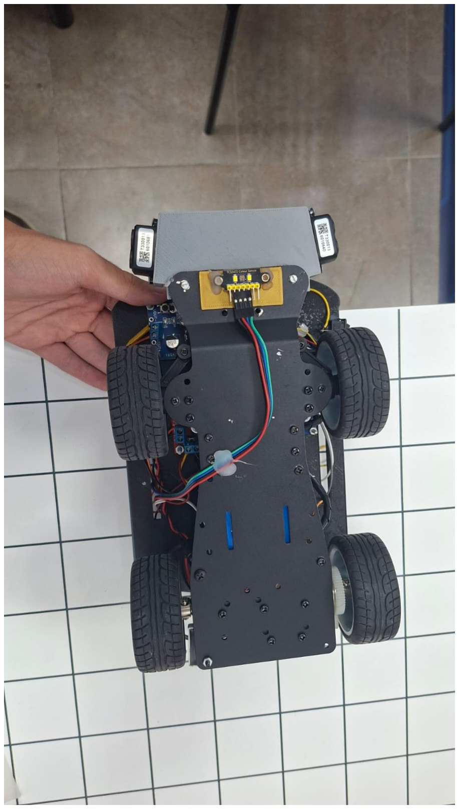
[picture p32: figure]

## Figure 5.6: Bottom image

68 | CHAPTER 5. PHOTOS

# 5.2 Team photos

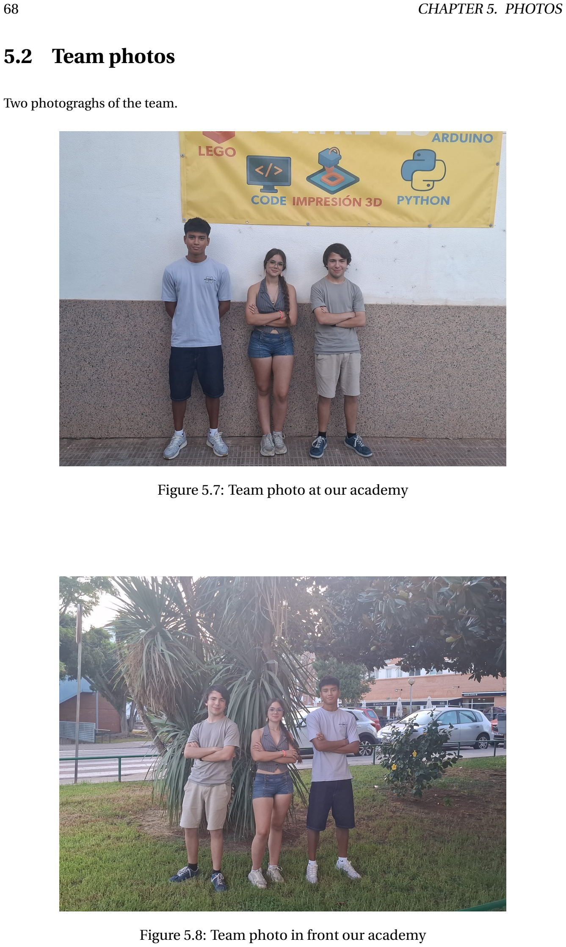
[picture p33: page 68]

Two photograghs of the team.

## Figure 5.7: Team photo at our academy

## Figure 5.8: Team photo in front our academy

### 6CHAPTER

# Videos

### We have uploaded two videos showing our robot completing each challenge. You can access

them via the following links.

- Open challenge: https://youtu.be/gIDQgGI8u58
- Obstacle challenge: http://www.example.com

69

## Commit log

2026-03-27 Add section for electronics and sensors in README
2026-05-29 Update sensor list in README
    Added VL53L1X and TCS34725 to the sensor list in README.
